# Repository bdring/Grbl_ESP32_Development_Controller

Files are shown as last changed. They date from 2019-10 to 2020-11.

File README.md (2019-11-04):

# Grbl_ESP32_Development_Controller
 A CNC controller to use and test Grbl_ESP32



This is a Grbl_ESP32 CNC Development board. This is a quick and easy way to use and test CNC on the ESP32 controller.

Grbl is a great CNC firmware that has been around for nearly a decade. It was originally designed for the Arduino UNO and basic 3 axis CNC routers, but it has been ported to other CPUs and was the basis for many other CNC and 3D printer firmwares.

The [firmware](https://github.com/bdring/Grbl_Esp32) was written using the Arduino IDE to make it as user friendly as possible. If you have experience with Arduinos, this will not be much different.

**I/O** - The ESP32 is very flexible allowing you to remap the the I/O features to alternate pins. Grbl_ESP32 is also far more flexible than Arduino Grbl for assigning pins to features. But, when you make a PCB, you force specific pins to specific features. To give some flexibility there are some shared pins. The SD Card shares pins with Mist coolant, Spindle Direction and Spindle Enable. These pins were chosen because they are very rarely used in DIY CNC. Full control of a variable speed spindle is still on a dedicated pin. If you really need the SD Card and some of those features, contact me. There are many alternative ways to do that. [See this wiki page for additional info on I/O](https://github.com/bdring/Grbl_Esp32/wiki/Setting-Up-the-I-O-Pins).

ESP32 brings the following features to small scale CNC.

- Powerful dual core processor running at 240MHz per core.
- 4MB of flash RAM
- Floating point coprocessor.
- On board Wifi.
- On Board Bluetooth.

The board has the following features.

- A very modular design - If the ESP32 or the stepper drivers get damaged, you can replace them.
- Socket for an ESP32 Dev board also known as NodeMCU 32S. Most 19 pin per side dev boards should work, just check the pins or ask me. Extra connector holes are positioned next to the NodeMCU 32S for test probing and to accommodate wider 19 pin modules.
- (3) Sockets for stepper motor drivers. These fit many types of drivers. The TI DRV8825 type is my favorite driver for this type of application. Micro-step selection jumpers are included. 
- Home/Limit switch connections for XY and Z axes. These also have R/C filters to eliminate high frequency noise from false triggering the switches.
- Control switch input connections for Feed Hold, Cycle Start, Reset and Door. These have filters as well as pullup resistors, because they are on inputs that do not have internal pullups.
- Spindle output for PWM (Speed).
- A micro SD Socket Note: Grbl senders do not support SD cards yet, but most have a manual console where the command is easily typed. The WebUI fully supports the SD Card.
- DC-DC power supply. There is a strong 3A DC-DC power supply to run the ESP32 if it is not connected to USB.

### Revision History

- Version 4.1
  - Same features, Changed pin numbers. GPIO_NUM_2 has an LED on some ESP32 modules. For some people that causes problems when it is used as an input (X Limit)

### Getting a pre assembled one.

This controller is generally available [for sale on Tindie]

### Donation

This project requires a lot of work and often expensive items for testing. Please consider a safe, secure and highly appreciated donation via the PayPal link below.



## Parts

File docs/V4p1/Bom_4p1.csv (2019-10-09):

RefDes | Value | Pattern | Quantity | Manufacturer | Mfg P/n | Link
C1, C6, C11 | 47u 35V | CAPAE-8.35x8.35h6.2 | 3 | Nichicon | UWX1V470MCL1GB | https://www.digikey.com/short/ptwvbr
C2, C3, C4, C5, C7, C8, C9, C10, C12, C16, C17 | 100nF | CAP_0805 | 11
C13 | 10uF | CAP_1206 | 1
C14 | 150pF | CAP_0805 | 1
C15 | 22uF 6.3V | CAP_1206 | 1
D1 |  | b340a-13-f | 1 | Vishay SS2P2L-M3/84A |  | https://lcsc.com/product-detail/Schottky-Barrier-Diodes-SBD_Jiangsu-Yutai-Elec-B340A_C64982.html
J2, J4, J7, J9 |  | HDR-1x4 | 4
J3, J8, J10 |  | HDR-1x8 | 2
J5 |  | HDR-1x19 | 2
J11 |  | PJ-102A | 1 | CUI | PJ-007 | https://lcsc.com/product-detail/Power-Connectors_Korean-Hroparts-Elec-DC-005C-20A_C84007.html
J20 |  | TF-01A | 1 | Korean Hroparts Elec TF-01A
JP1, JP2, JP3 |  | HDR-2x3 | 3
L1 | 4.7uH | Inductor 06030 | 1 | Chilisin Elec | MHCI06030-4R7M-R8 | https://lcsc.com/product-detail/Power-Inductors_Chilisin-Elec-MHCI06030-4R7M-R8_C108295.html
R1, R2, R3, R4, R17, R18 | 10k | RES_1206 | 4
R5, R14 | 100k | RES_0805 | 2
R6, R7, R8, R9, R10, R11, R12, R13 | 100 | RES_1206 | 8
R15 | 40.2k | RES_0805 | 1
R16 | 210k | RES_0805 | 1
U1 | ESP-32 | ESP-32 NodeMCU 32S | 1 | (2) 1x19 Female Sockets
U2, U3, U4 |  | StepStick | 3 | (2) 1x8 Female Header
U5 | MP1584EN | MP1584EN | 1 | Monolithic Power Systems | MP1584EN-LF-Z | https://lcsc.com/product-detail/DC-DC-Converters_MPS_MP1584EN-LF-Z_MP1584EN-LF-Z_C15051.html
U6 | TXS0101DBVR | TXS0101DBVR | 1 | TI | TXS0101DBVR | https://lcsc.com/product-detail/Logic-ICs_TI_TXS0101DBVR_TXS0101DBVR_C132604.html

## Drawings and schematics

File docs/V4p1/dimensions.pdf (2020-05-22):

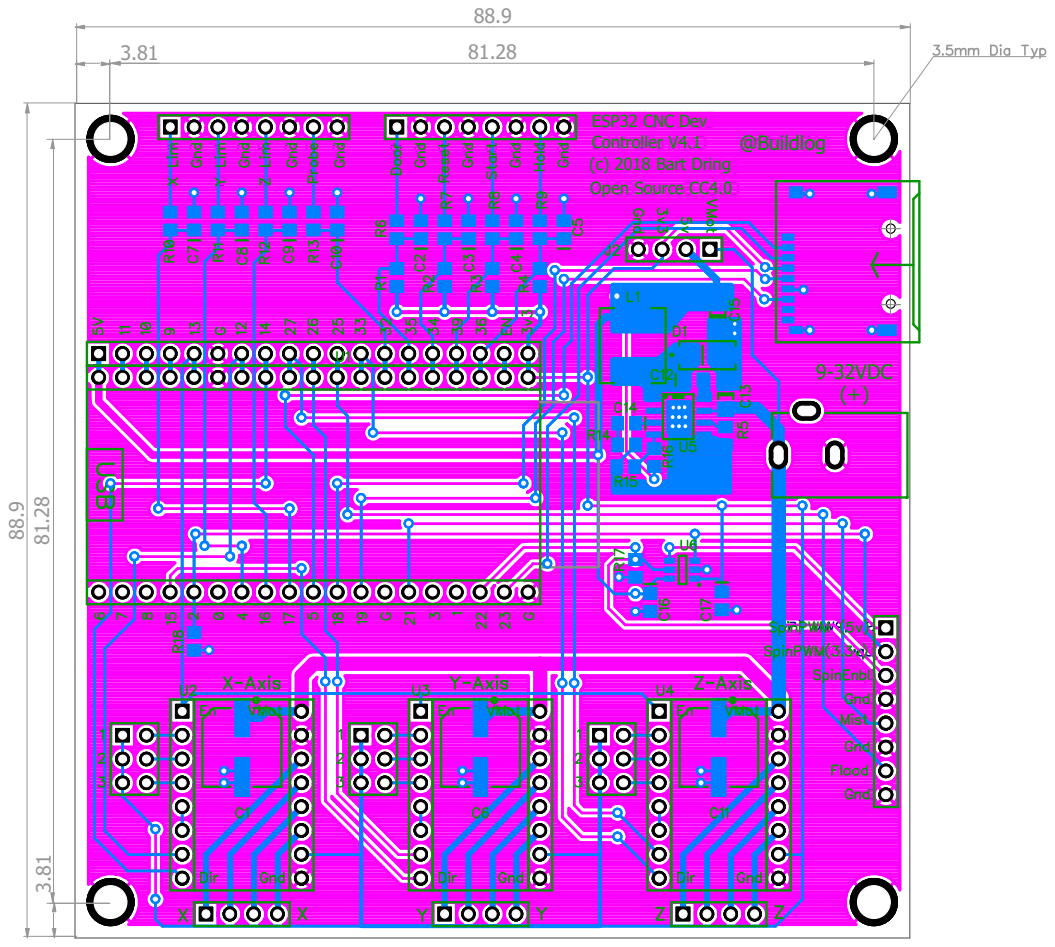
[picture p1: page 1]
ESP32 CNC Dev

Controller V4.1 @Buildlog
(c) 2018 Bart Dring
Open Source CC4.0

9-32VDC
(+)

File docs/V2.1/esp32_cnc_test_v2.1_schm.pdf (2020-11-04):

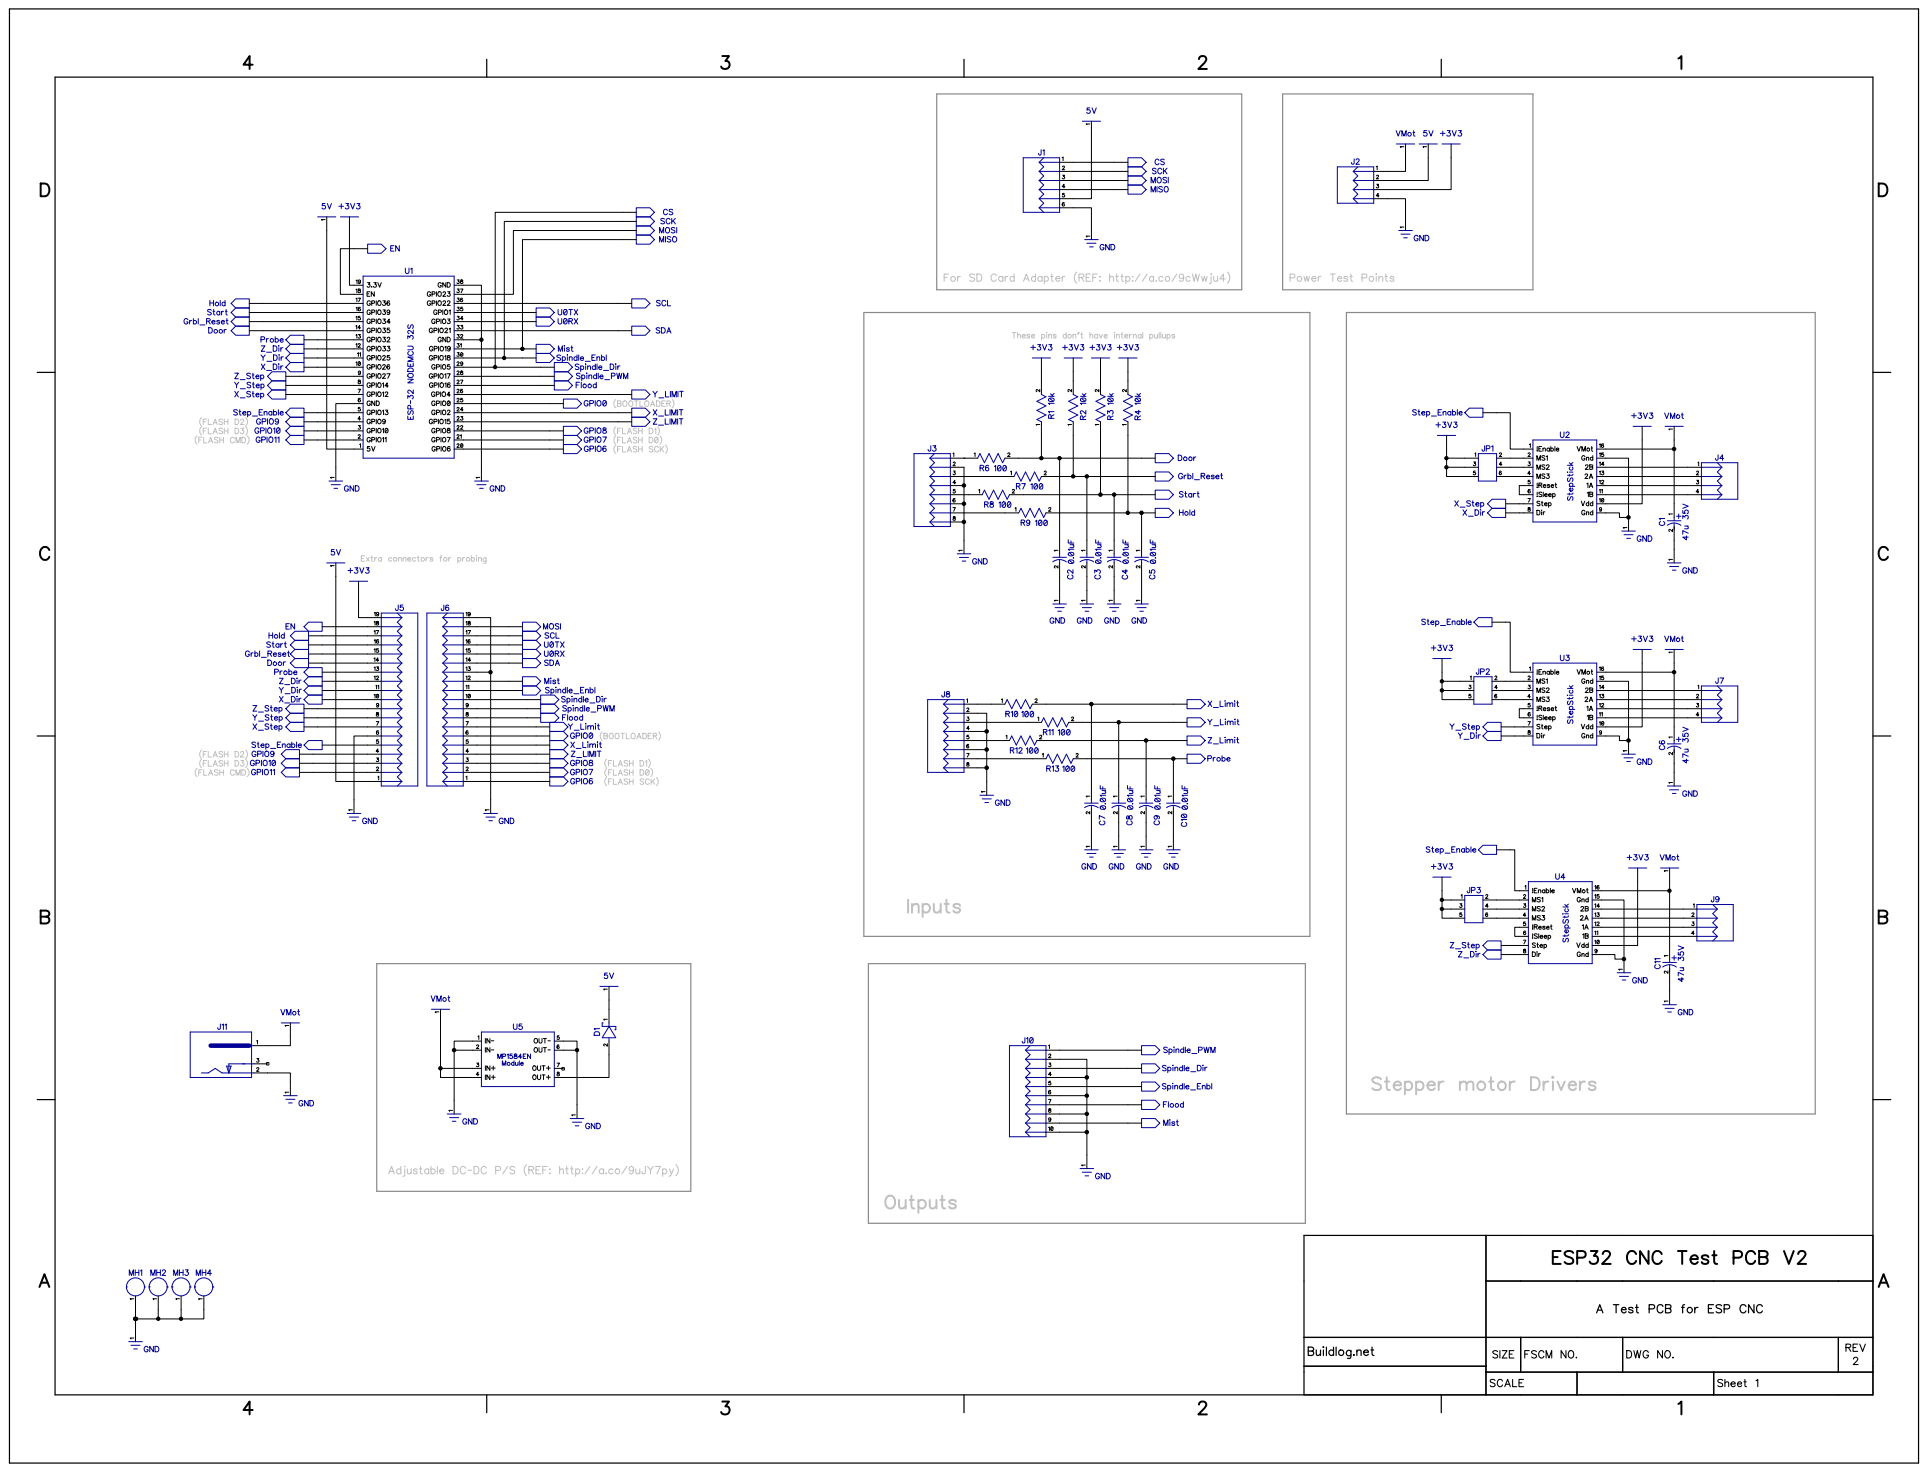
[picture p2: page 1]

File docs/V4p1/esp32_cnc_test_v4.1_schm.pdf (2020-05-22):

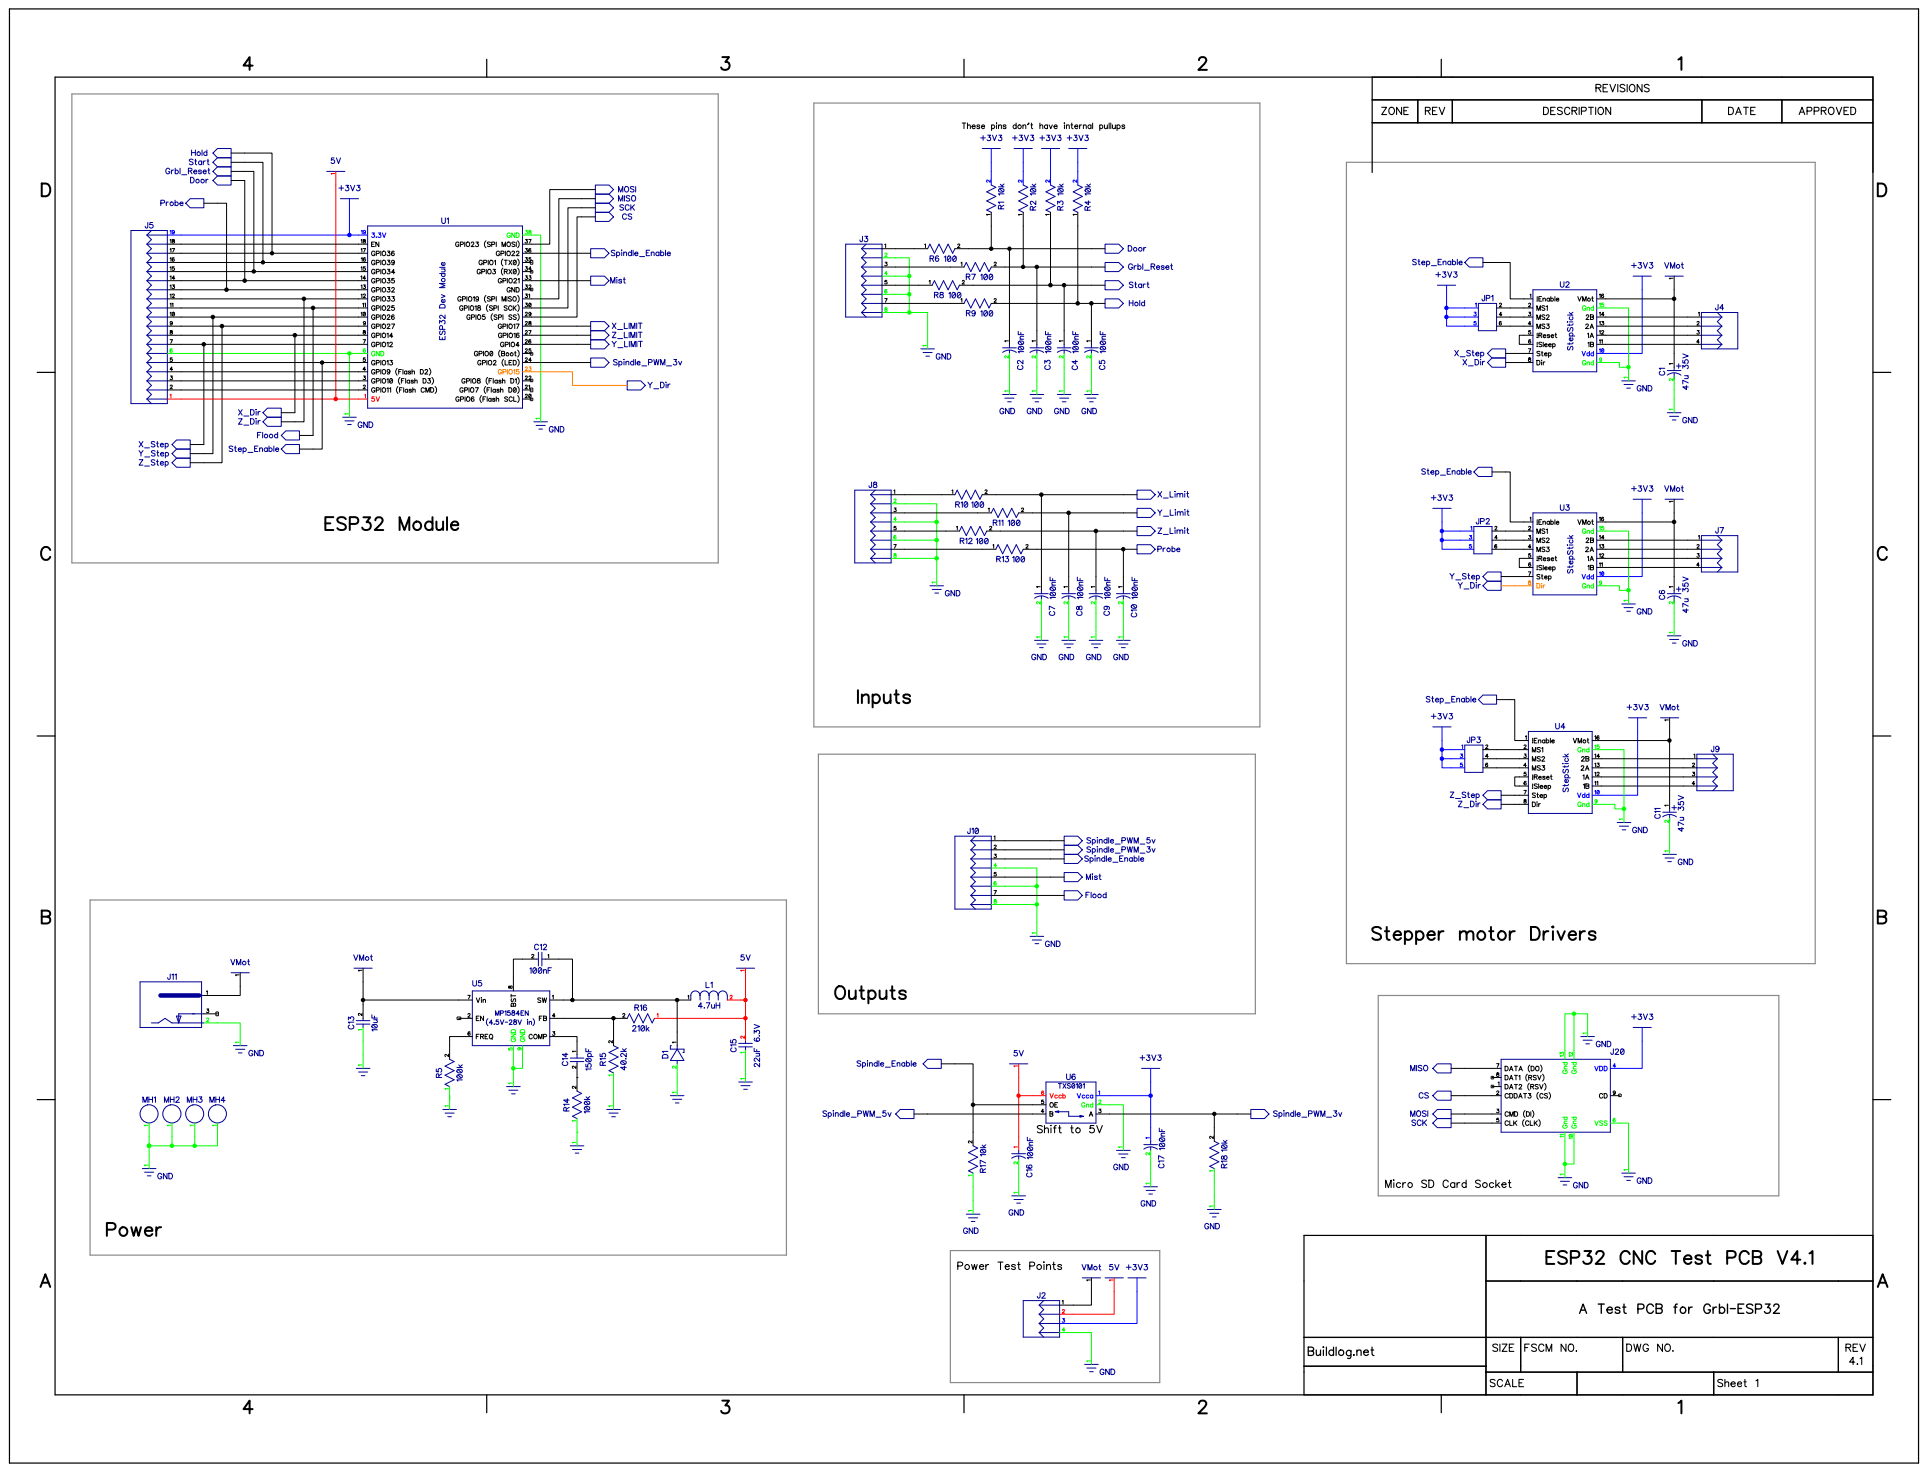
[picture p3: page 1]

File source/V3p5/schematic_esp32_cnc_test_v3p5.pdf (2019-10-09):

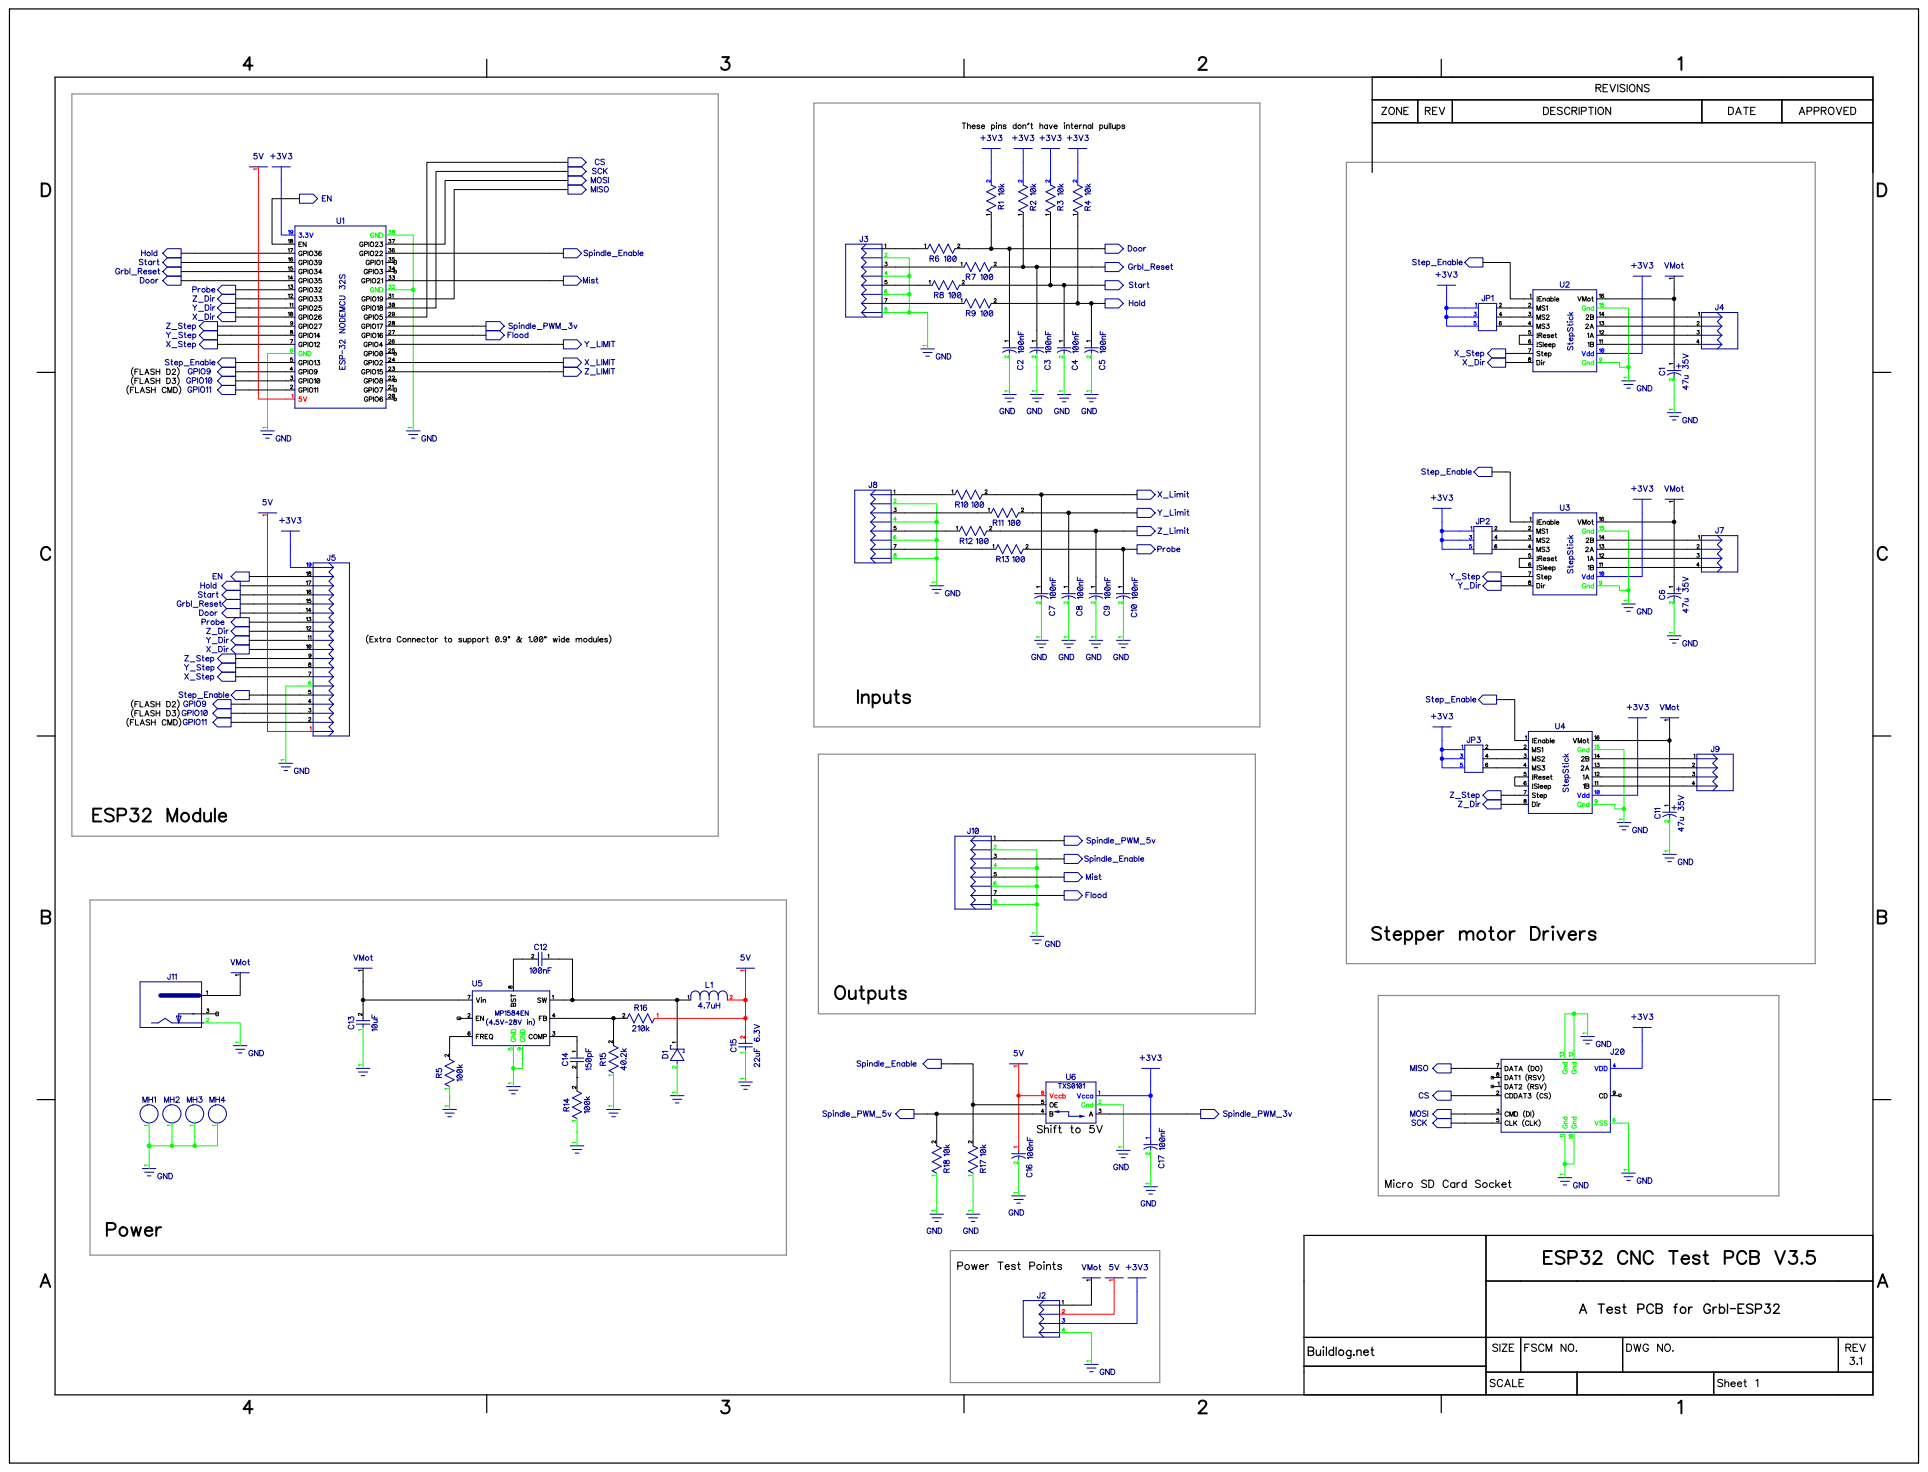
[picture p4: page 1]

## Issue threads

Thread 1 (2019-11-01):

Need a Gernerates pick and place files

jasinghuang, 2019-11-01:
Hello! I'm going to make your version of control borad(https://github.com/bdring/Grbl_ESP32_Development_Controller) to replace my old uno control board, I am trying to make a pcb with SMT,and the seller need ’**Gernerates pick and place files**‘, and I can not find it in the zip.

Thank you!

bdring, 2019-11-01:
I don't have a pick and place file for it. How many are you making?

jasinghuang, 2019-11-01:
> I don't have a pick and place file for it. How many are you making?

I am making only 2 boards, one for insurance.

tpickett, 2020-07-30:
jlpcb will do most of the work for smt if this is added. easy to order 5 of them for cheap. would love to support on Tindie though ;)

bdring, 2020-07-30:
[Added](https://github.com/bdring/Grbl_ESP32_Development_Controller/blob/master/gerbers/V4p1/V4p1_centroid.csv)

guestisp, 2022-04-14:
For jlbpcb , the BOM and the pick&trace file has to be modified. In example, in the BOM, some components are missing the description end even the columns title and positioning is not good for jlbpcb

Closed 2020-07-30.

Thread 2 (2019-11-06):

Driving MOSFETs directly with the TXS0101

shreeramlive, 2019-11-06:
According to the output of the **TXS0101** IC, the max output current is rated as **100mA**.
_[ Continuous current through VCCA, VCCB, or GND = ±100 mA ]_
So can we drive a **MOSFET** or light up up a **few LED**s directly from the output of level shifter?
Would this cause any **damage** to the **ESP32** board?
Would there be better protection to the board if all the **outputs** are routed through voltage shifters (something like TXS0104 for more pins) ?

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

And one more doubt, what happens when a pin ( configured as **output** ) gets **shorted with ground**? Like connecting a **limit switch** wrongly a to pin which is mapped for **Spindle output**.

bdring, 2019-11-06:
The TXS0101 can switch current to gnd. It uses a 10k pullup for 5v.  You could drive some LEDs by connecting the low side of the LED. You can't drive much with the 5v signal.

shreeramlive, 2019-11-07:
Thanks for the info @bdring

Closed 2019-11-07.

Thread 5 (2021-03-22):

Motor Driver : How to interface with 3.3V logic level

RepRapThailand, 2021-03-22:
Hello,

I try these  drivers with GRBL on Arduino UNO and all four drivers can spin motor but when I try with ESP32 only two drivers TB6560 and Black driver can spin motor.

 Best Regards,

###  **TB6560**
https://wiki.keyestudio.com/Ks0318_keyestudio_Tb6560_Stepper_Motor_Drive_Board

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
###  **TB6600**

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

###  **TB67S109-OC**
https://github.com/makerbase-mks/MKS-Big-Current-Driver/blob/master/MKS%20TB67S109%20OC/MKS%20TB67S109-OC%20V1.0_001/MKS%20TB67S109-OC%20V1.0_001%20SCH.pdf
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

### **BLACK Driver**

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

evaldo-seara, 2023-10-16:
I need to connect this driver in 3v3, how did you do it?

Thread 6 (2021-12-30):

TXS0101DBVR IC

sarhadi, 2021-12-30:
Hello,

Great job 👍
As far as I know, TXS0101DBVR is new component since the 3rd version,
& I couldn't find it in the market in my region.
What does this "Voltage Level Translator" actually do in this version?
Is there any other component to replace with TXS0101DBVR ?
Any Chinese or something cheap ?

Regards,
Ehsan,

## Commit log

2019-11-04 Added version 4.1
    [Bom_4p1.csv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]
2020-07-30 Added pick and place data
    [V4p1_centroid.csv]
